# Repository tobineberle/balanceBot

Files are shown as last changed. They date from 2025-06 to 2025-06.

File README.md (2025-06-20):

# balanceBot-v0

## **Introduction**
Over the past few years I have found myself growing increasingly nerdy in all matters engineering related (and trains too for that matter), and it so happens that this interest has had a direct correlation with my desire to build a cool engineering project. I have been fascinated by the [inverted pendulumn problem](https://en.wikipedia.org/wiki/Inverted_pendulum) since my University days, and with some free, unemployed time on my hands I decided to build something influenced by it- the self balancing robot.

### **Goals**
The goal for this project was to build a self-balancing robot from the ground up. No kits, no libraries, no pre-made parts (lets talk about breakout boards later). This was a challenge to approach every aspect of the robot from ground zero with my own engineering decisions and mistakes (so, so many mistakes). There will be stretch goals for subsequent versions of this project but these will be discussed further below under their specific design category. 

### **Parts List**

A quick summary of the parts used. Consumables such as wires and screws are not listed.

| Part Name | Quantity|
|-|-|
|STM32F401RE Nucleo Board | 1 |
|A4988 Stepper Driver | 2|
|SEN0142 MPU6050 Board | 1 |
|SM-42HB34F08AB 12V/1.33A Stepper Motor| 2|
|1998 5MM SHAFT M3 MNTG Hub| 2|

### **Results**
You don't need to scroll all the way down, here is a gif of the robot doing a happy little balancing dance:

Robot

From stress testing it can balance for over five minutes. This is the cutoff where the motors are too hot and the frame begins to melt. It has good setpoint tracking with only minor oscillation and good disturbance rejection (not demonstrated in gif).

### **Next Steps**

Some big future goals I have for the project:
- Integrate all components onto a PCB
- Add bluetooth steering
- Refine the system control (cascade or LRQ)

Stay tuned!

## **Design**

## Mechanical

My approach to the frame design was straightforward: I wanted the robot to be around 20-30cm tall and it needed to be wide enough to accomodate my protoboards. As I have been getting into 3D printing, I chose to design it all in Fusion360. All the following parts were designed in CAD and the stl's are in on github. I won't include the 3D files because I'm pretty sure my file structure/ogranization in them is atrocious.

### **Frame**

I wanted the frame to be modular so that I could print and test the fit of pieces without wasting time or PLA. To accomodate this I added slots on the frame sides so that the middle brackets could slide in. The middle brakets are further secured by pressing a square nut into the holes in each corner before seating them, then screwing them into place. All hardware used to secure the brackets is m3 as its what I had easiest access to.

The middle brackets have slots down the middle for modular mounting of PCBs later. The side brackets have flames down the middle for speed.

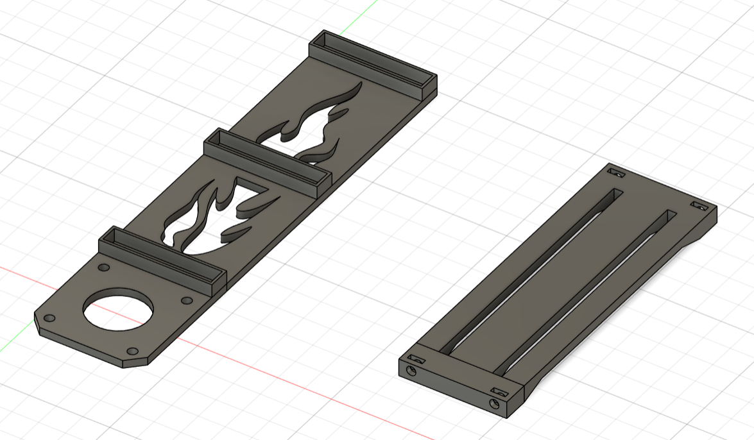
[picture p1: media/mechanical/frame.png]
frame


*Frame Design*

### **Wheels**

Not too much design aspect for the wheels, just had to make sure they fit the aluminium mounting hubs I ordered. 

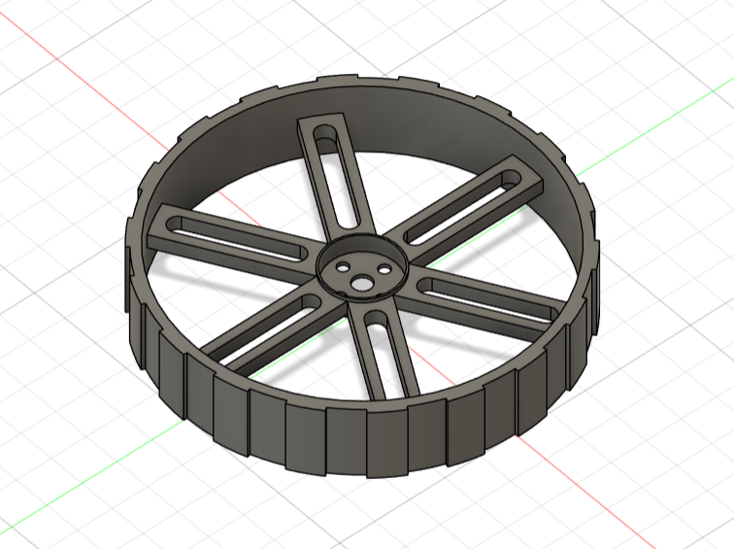
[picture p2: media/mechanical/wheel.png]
wheel


*Wheel Design*

As I was making custom wheels, I needed custom tires to fit them. After researching many methods, the best and most cost effective I found was to make them using hardware store silicone (mono silicone sealant) mixed with cornstarch. Through some messy experimentation, I found a good ratio of silicone to cornstartch was 10:1 and that about 100g silicone + 10g cornstarch was enough to fill my tire molds and had about a 24 hour curing time. The tire mold went through two iterations of design in order to make it easier to remove the tires wihout ripping them. Not many photos here as it was messy.

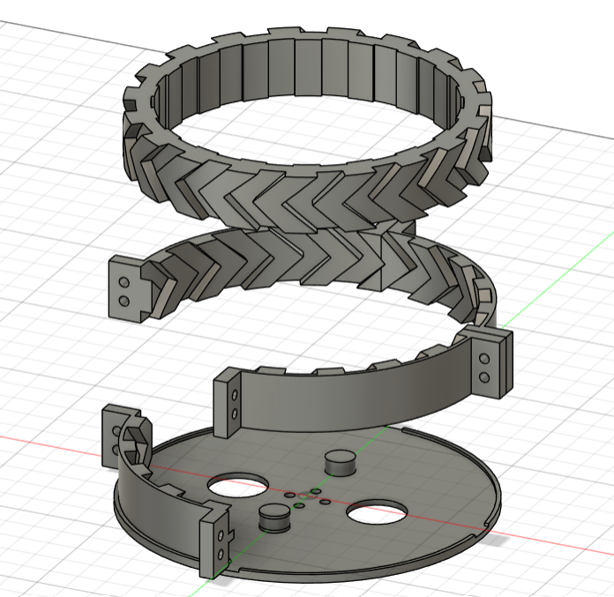
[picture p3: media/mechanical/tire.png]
tire


*Tire/Mold Design*

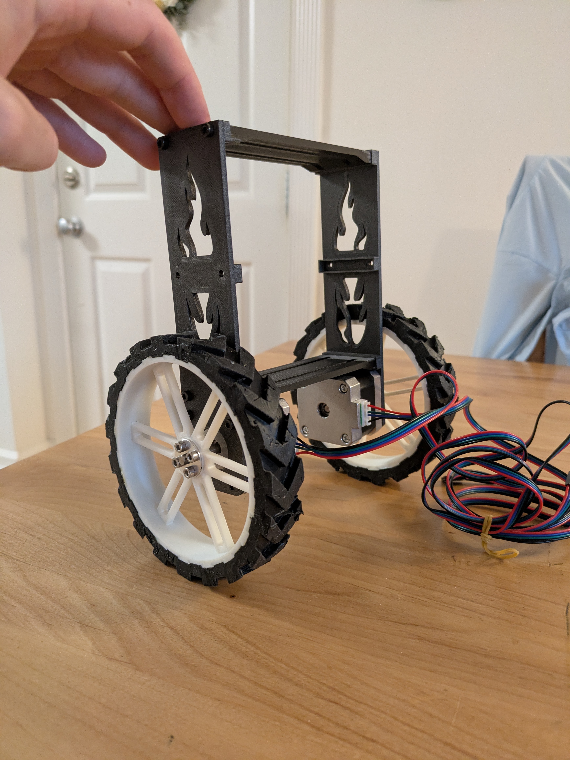
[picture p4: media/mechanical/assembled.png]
assembled


*Assembled Frame*

### **Improvements**

- Frame needs to be printed in a stronger material. The PLA begins to melt after running the motors for more than 5 minutes continuously
- Tires could be redesigned to have less aggresive tread as it would make them easier to remove from the mold. Holy hell taking them out was stressful 
- If I had access to a different material to print the tires with I would 3D print them directly to save hassle
- The mounting bracket system will likely be redesigned for V1 as I get custom PCBs, but it is modular and works well in the meantime

## Electrical

Here is where we talk about using eval boards for components like the A4988 drivers or MPU6050 inertia measurement unit. For V0 of this project, I thought it was more important to get an inital prototype actually working rather then spending months in the weeds doing design work that has already been completed. I have plans to make a microcontroller integrated PCB for the robot, so integrating these other chips would fall within this stretch goal. Good is better than perfect if it means you get stuff done.

### **Part Selection**
#### MicroController

I chose to use STM32 as I wanted to work within an industry accepted environment (sorry arduino). This also meant I got to practice and improve my bare metal programming skills and dry out my eyes reading datasheets. It was also a goal of mine to write libraries for all my components from scratch (except for HAL drivers as I've done this before) and this platform supported this goal by having nothing pre-existing readily available.

#### Motors

NEMA17 stepper motors were chosen due to the ability to directly control their position by commanding steps. To size them properly, I looked for a set that had sufficient torque rating that was over double what I calculated for my robot. I also looked for a higher voltage motor so I could power both the motor and the electronics from one power source.

#### Driver

From research the A4988 is a common motor driver that can support up to ~1.2A of current which is very close to the max rated current of ~1.33A of my motors. 

#### Inertia Measurement Unit

Again, from research the MPU6050 is a common IMU to use. 6DOF was plenty for only neededing to detect pitch and y angle.

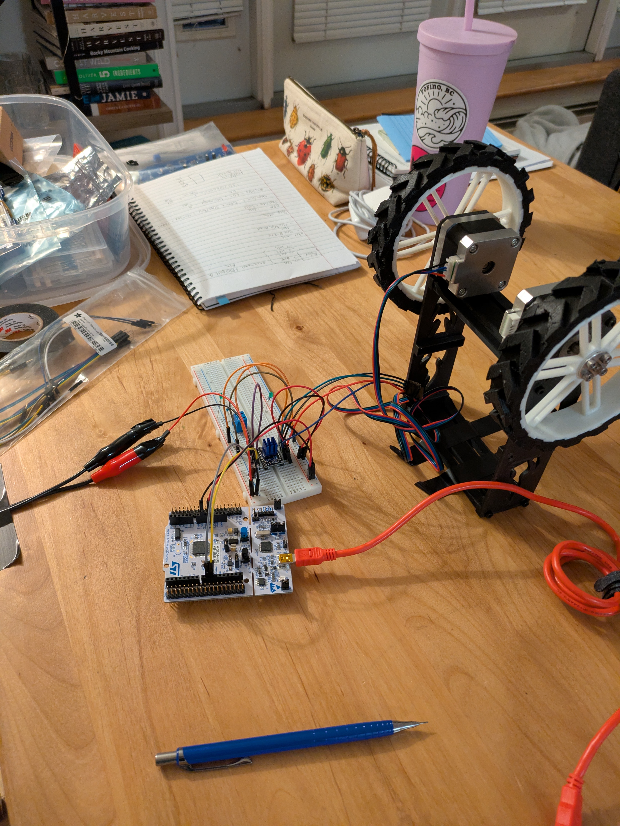
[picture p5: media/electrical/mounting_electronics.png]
elec


*Electronics Breadboarding*

### **Power Distribution**

A little power distribution circuit designed around the LM7805. The LM7805 can regulate up to 30V into 5V which can power the STM32 and peripherals. This lets me run everything from my 12V wall source or a single 4S Lipo battery. LED's are hugely useful for visual feedback that your system is working as intended. This ciruict was soldered onto protoboard along with breakout pins for the A4988 and MPU6050 boards. As mentioned in this sections header, V1 will hopefully incorporate all the components onto a dedicated PCB along with multiple power input methods. Note I only used resistors close to the values shown, just not remembering true values at time of writing this.

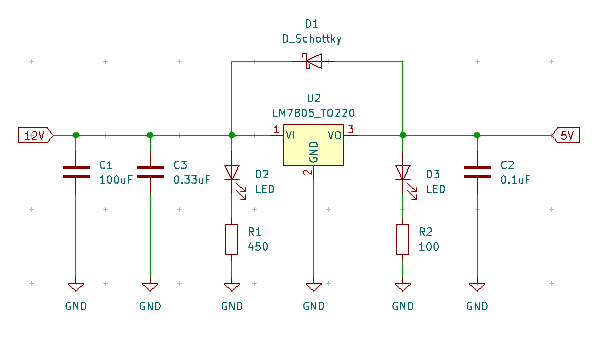
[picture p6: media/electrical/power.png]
power


*Power Distribution using LM7805*

### **Improvements**
- Integrate all components into a single PCB (V1)
- Add multiple methods for power connection and reverse voltage protection
- I haven't actually caluclated a power draw for this sytem yet, so am guessing at the mAh of the batteries I need to order

## Software

Prepare for a long section with diagrams. Writing these libraries and troubleshooting code took propably twice to three times as long as the rest of the project put together. This was probably the most valuable section of the project (so far) for me as it really helped improve my bare metal knowledge. For running a real time control system you need to have around 100-200 Hz loop frequency (5-10 ms loop times).

### **MPU6050 Library**

The MPU6050 communicates with the STM32 over I2C. Sending/reading data from the device is generally easy, using HAL_Read you can read directly from the MPU6050 registers. 

#### Accelerometer and Gryo Data

Straight forward section, just read from registers specified on the MPU6050 datasheet. Simple as.

#### Accelerometer and Gryo Angles

X/Y/Z or Pitch/Yaw/Roll angles can be calculated from your accelerometer and gyro readings. Accelerometer angle is based on trigonometry between the acceleration axises and the gyro angle is based on time elapsed between measurements. Implementations can be found in source code. Rule of thumb for these readings is that angles from your accelerometer will be noisy and angle from you gyro will drift over time. 

#### Kalman Filter Angle

To overcome the noise and drift issues in direct angle calculation, we use the kalman filter. This filter lets us predict the state of a system based on known readings and our estimation of error from both our calculation of the system state and our measurement of the system state. Using a kalman filter is preferable here as values can converge more quickly than averaging over time allowing us to use the filtered angle immediately. As shown below, it is quite amazing how well this works- notice how we have a noisy accelerometer signal and gyro drift and how these are filtered into a smooth signal.

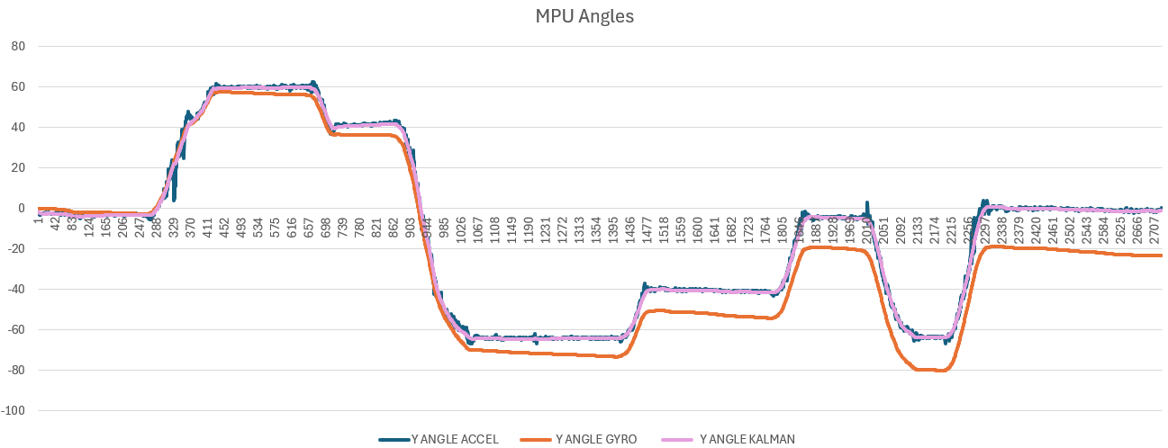
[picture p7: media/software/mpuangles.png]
mpu


*MPU angle comparison*

### **PID Library**

Controls is awesome and if you don't love controls you should because it's awesome. The self balancing robot is technically a non-linear system and thus is a good candidate for a linear quadratic regulator (LQR) which I might implement in a later version. However, PID is also a very reliable method of control and with proper tuning can give excellent results even for non-linear systems. PID is also much simpler to implement in code and I had prior expereince doing it. 

#### PID Updating

This method just updates a PID loop based off its initialzed set point, current value, loop time, and whether we are including derivative filtering. As the block diagram below shows, the code functions as a regular PID loop. Something that is not always common in these systems is the low-pass derivative filtering to smooth noise. From testing, the derivative noise was badly amplified that the robot would shake uncontrollably without any sort of filter on this error. 

Some notes for tuning these gains:

- P: Tune until the robot can catch itself but begins to oscillate back and forth
- D: After P, tune until oscillations are removed and minimized
- I: After D, tune if the robot is drifting in a particular direction. Only tune slightly and if needed.

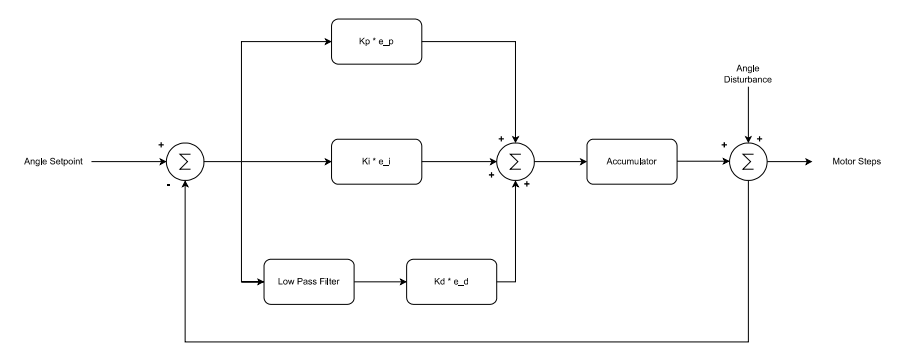
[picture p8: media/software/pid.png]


*PID Control with Low Pass Filtering*

#### Low Pass Filtering

The low pass filter is used to smooth an output based on previous input data. It has an alpha scaling factor from 0.1 (very smooth) to 1 (no smoothing). Some examples of PID logs with and without smoothing are shown below for dramatic impact.

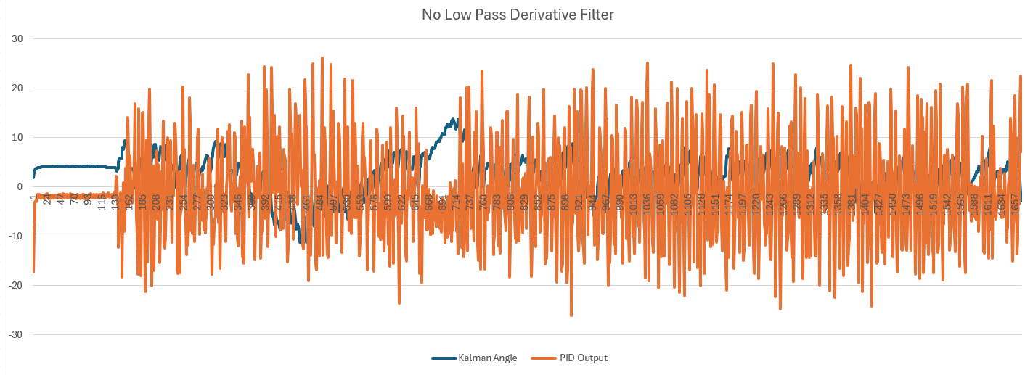
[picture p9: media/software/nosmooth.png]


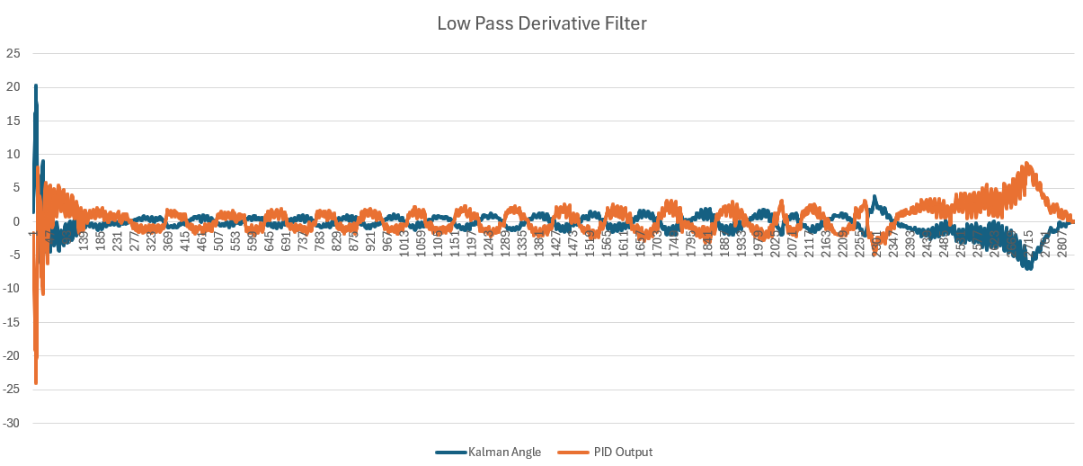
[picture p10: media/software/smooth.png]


*Difference between without and with low pass derivative filtering*

### **A4988 Library**

I wrote an A4988 C library for the STM32F401RE and this helped me get a really good basis of state-based programming, timer setup, and interrupt handling. This was the final piece after implementing the previous two libraries and I thought it would keep going quickly! I was devistatingly wrong. Writing non-blocking motor control code was incredibly tedious, and I spent a lot of time troubleshooting and reading through some other peoples work online. Specifically the following mentions:

[Laurb9's Arduino Cpp Code](https://github.com/laurb9/StepperDriver)

[ErniW's Cpp Code](https://github.com/ErniW/Stepper-motor-bare-metal-STM32)

[Patrick's C Code](https://gitlab.com/rickpat/stm32_a4988)

Now for A4988 operating theory. The A4988 sends motor step when it sees a rising edge on its STEP pin and then needs a 1us settling time before the next pulse. This means the driver can be driven by PWM from the STM32 timer channels or through timer based GPIO triggers. Each of the following different states "modes" controls the PWM frequency in a slightly different way.

For state-based design, I may have gone overboard. Without a pre-planned state diagram, I found myself getting more and more convoluted as my work progressed. The resulting states and their related substates are in the diagram below and I will talk breifly about them in the following sections.

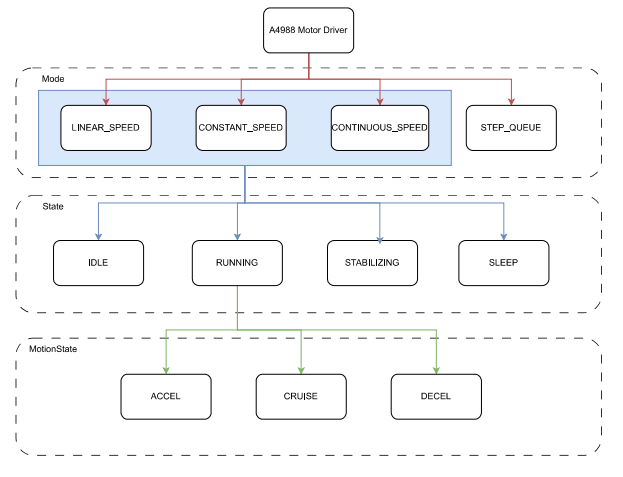
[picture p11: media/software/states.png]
states


*Breakdown of A4988 states and substates*

#### Constant/Linear Speed Modes

This was my first attempt at motor control and was based on what I learned from other motor source code. We set the timer to PWM and then vary the timer length (ARR) to change the motor speed. Every time the motor meets the control capture value it creates an interrupt in which we update parameters such as: position, next cycle speed, steps remaining. While this works really well for time invariant pre-planned moves, it lags in real time systems and was not even remotely close to balancing the bot.

Constant Mode: Send a set number of steps to move and the motor will run at the preset RPM for all steps

Linear Mode: This gives the motor a trapezoidal or triangular speed profile so that it accelerates, cruises, then decelerates over the number of steps you provide it. 

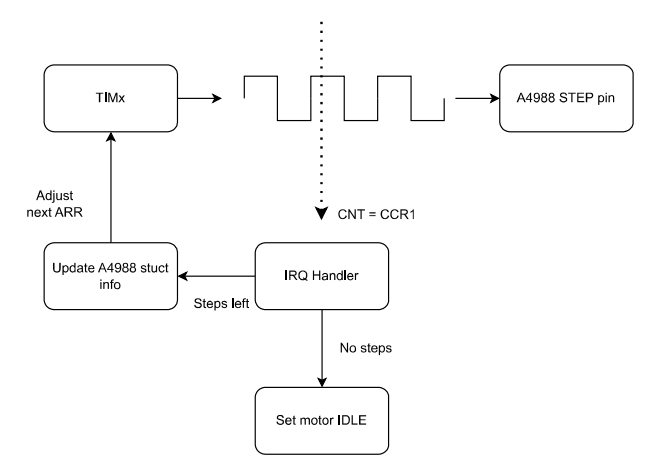
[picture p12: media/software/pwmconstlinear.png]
pwmconstlinear


*Constant/Linear speed diagram*

#### Continuous Speed Mode

The second attempt at motor control was a continuous speed mode, where the motors are constantly running and you just update the RPM. In theory this should work and I probably could've gotten there with it but I ran into MAJOR timer issues. Firstly, I had a timer issue where going from a high -> low rpm would cause the motor to freeze due to the timer ARR not updating and then another CCR event not triggering. I solved this by forcing an auto reload and CNT to 0 so that the timers would function properly for PWM.

This fix caused my second issue in which by forcing a reload and the CNT to 0 I would cut off the PWM cycle of some PWM pulses if my main loop was executing too fast. This was an issue as the main loop needed to run at speeds that prohibited this style of motor control from working at RPM's less than around 30 (depending on microstepping levels). The structure for this looks similar to the diagram in constant/linear. All in all, I probably worked on this mode for 30-40 hours before abandoning it. It still works for continous speed, just not for high update rate applications.

Here are the timing tables I made to diagnose the second issue. These are also useful for if you want to use this mode for some reason and need to know its limits.

*TIMING VALUES FOR REALISTIC RPMS FOR MICROSTEP LEVELS TABLE*
|MS SCALE| MIN ARR 16 Bit [us]| MAX ARR 16 Bit [us]| MIN ARR 32 Bit [us] | MAX ARR 32 Bit [us]
|- |- | -| -| -|
| 1 | 1500 | 60000 | 1500 | 300000 |
| 1/2 | 750 | 50000 | 750 | 150000 |
| 1/4 | 375 | 37500 | 375 | 75000 |
| 1/8 | 187 | 37500 | 187 | 37500 |
| 1/16 | 93 | 18750|  93 | 18750 |

#### Step Queue Mode

The holy grail of motor control. After a lot more research and pondering I started step queue method. By running a timer at a constant frequency (10KHz) and using the IRQ handler to choose when to toggle the output pin (i.e. use GPIO instead of TIMx Channels) we can control the amount of steps we are taking almost in real time. The kicker here is that the IRQ handler needs to be fast:

 ```"Interrupts shall be quick and simple"```

 When we mean fast, we mean on the order of a few us, as there is only 100us inbetween interrupt calls. For this, I stripped down my IRQ handler to the essentials and used some atomic functions and direct register writes to make the process faster.

 <img src="./media/software/stepq.png" alt="stepq" width="600"/>

*Step Queue diagram*

FINALLY success! As a final safety precaution, I created another table to limit the number of steps fed into the step queue for each iteration of the main loop, effectively capping the maximum RPM. The below table shows the max steps allowed to queue for different max RPMs at different main loop speeds [Hz]. This is showed for sixteenth microstepping and the values vary for different resolutions of full steps.

 <img src="./media/software/maxrpm.png" alt="maxrpm" width="600"/>

*Step Queue Max RPM for 1/16 Microstepping*

### **Improvements**
- I'm just going to spend a month in a hole refactoring my code and bug testing

 <img src="./media/workstation.png" alt="workstation" width="600"/>

*Cozy workstation shot if you made it this far*

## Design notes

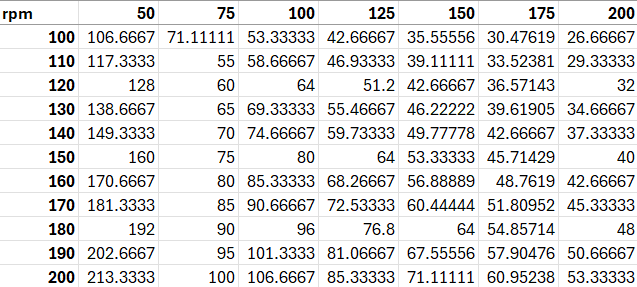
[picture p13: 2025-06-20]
media/software/maxrpm.png

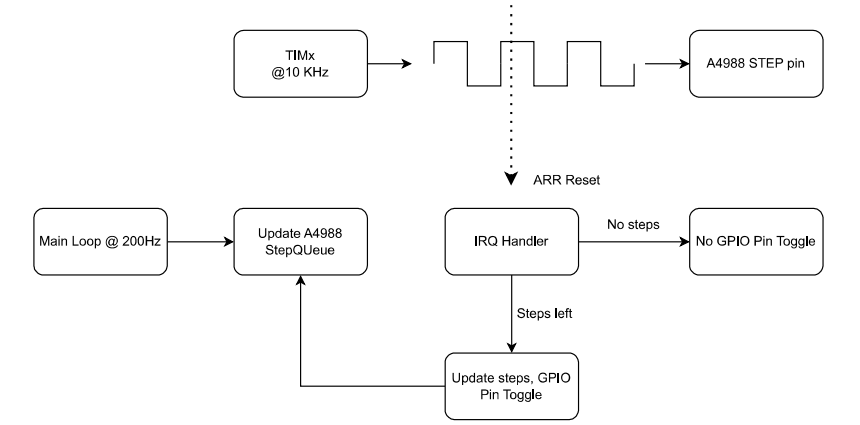
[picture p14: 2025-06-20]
media/software/stepq.png

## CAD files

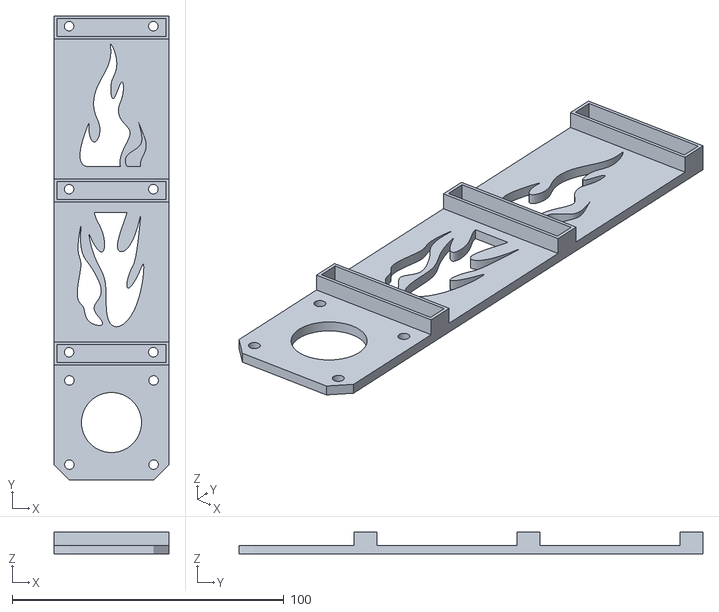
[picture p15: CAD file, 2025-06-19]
Models/Frame/frame-v1.stl
42.3 x 170.8 x 8.00

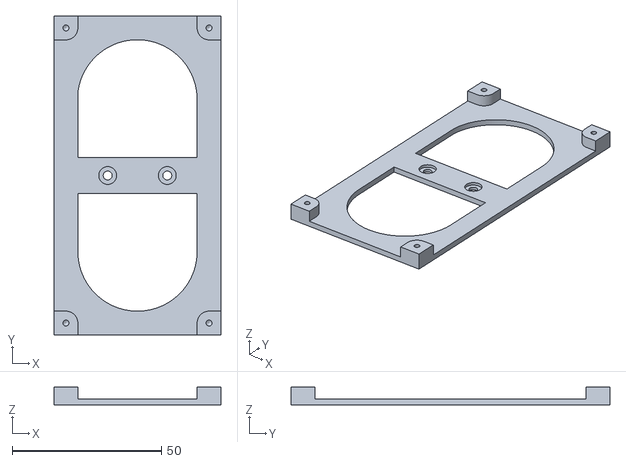
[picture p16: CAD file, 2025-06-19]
Models/PCB Mounts/pcb_mount_v0.stl
56.0 x 107.0 x 6.00

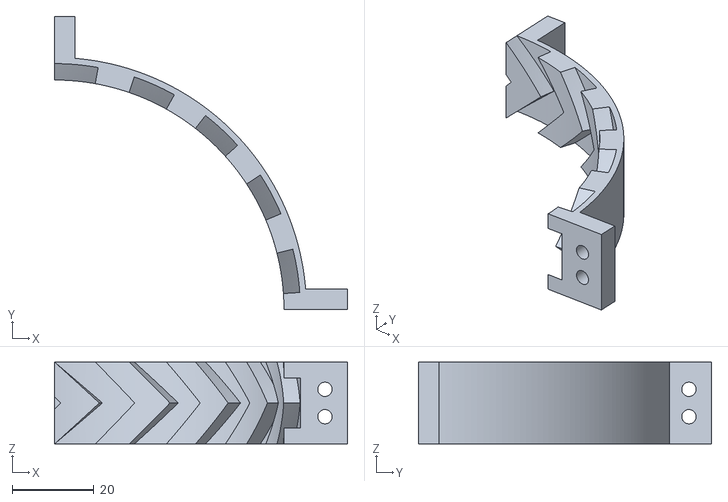
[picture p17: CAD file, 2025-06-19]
Models/Wheels/side-mold-I-v0.stl
71.5 x 71.5 x 20.0

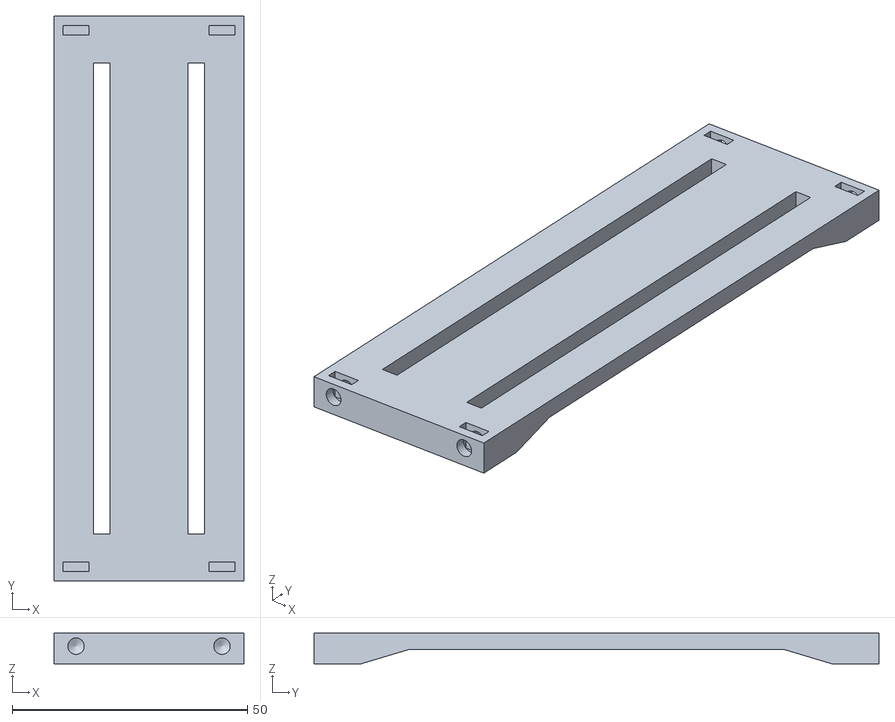
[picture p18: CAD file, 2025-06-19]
Models/Frame/mount-bracket-v1.stl
40.3 x 120.0 x 6.50

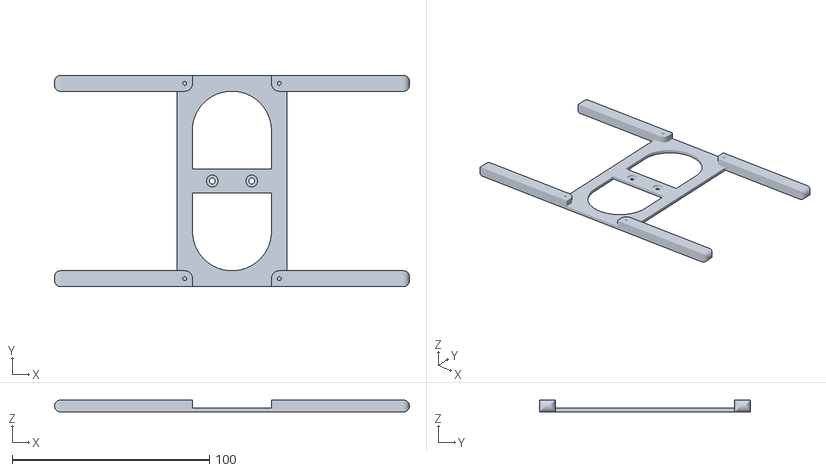
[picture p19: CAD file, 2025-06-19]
Models/PCB Mounts/pcb_mount_arms.stl
180.0 x 107.0 x 6.00

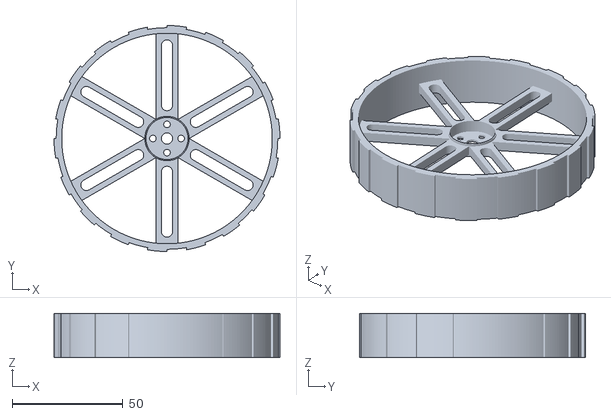
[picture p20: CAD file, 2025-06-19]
Models/Wheels/wheel_v1.stl
102.0 x 102.0 x 20.0

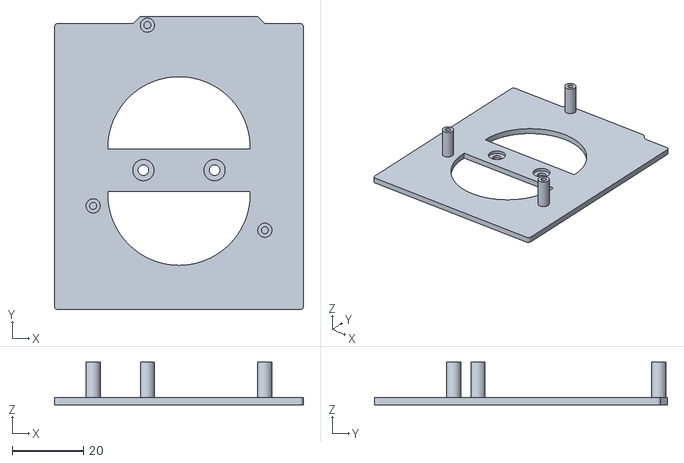
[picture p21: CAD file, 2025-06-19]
Models/PCB Mounts/stm_mount_v0.stl
70.0 x 82.5 x 12.0

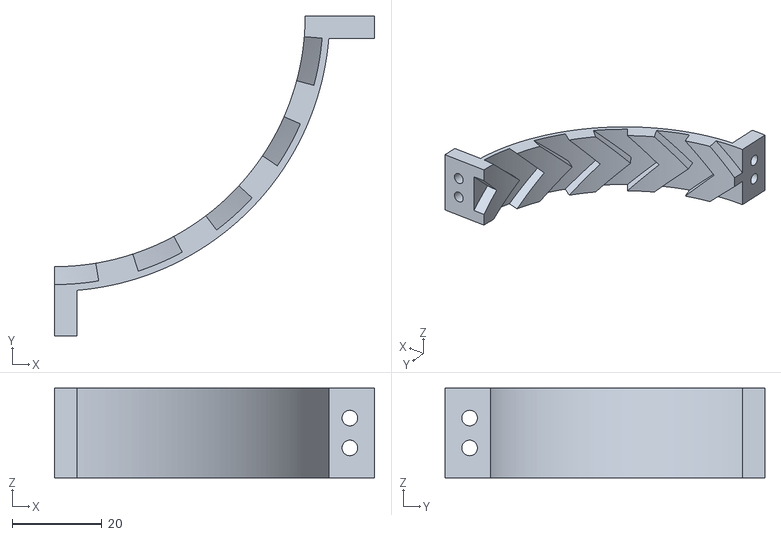
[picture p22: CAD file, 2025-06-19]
Models/Wheels/side-mold-IV-v0.stl
71.5 x 71.5 x 20.0

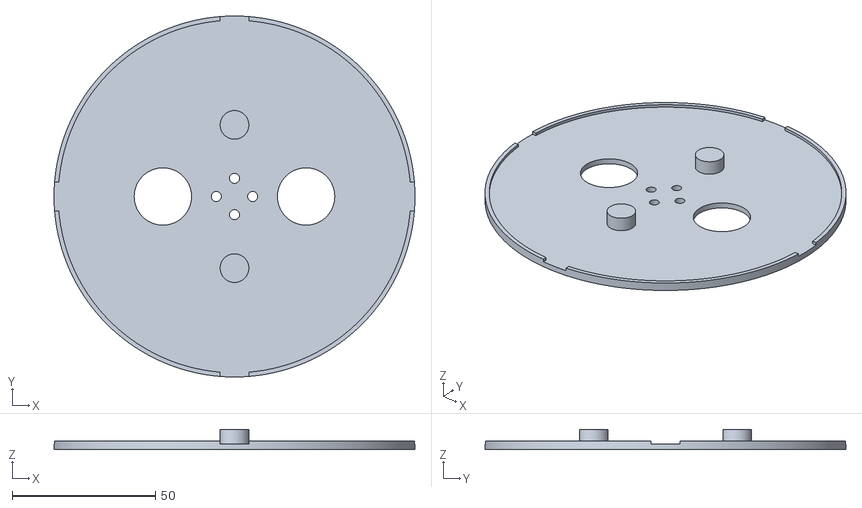
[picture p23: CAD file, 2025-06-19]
Models/Wheels/top-bottom-mold-v1.stl
126.0 x 126.0 x 7.00

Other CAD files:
Models/Wheels/side-mold-III-v0.stl
Models/Wheels/side-mold-II-v0.stl

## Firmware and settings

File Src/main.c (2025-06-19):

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
/* Includes ------------------------------------------------------------------*/
#include "main.h"

/* USER CODE BEGIN Includes */
//#include <a4988.h>
#include <mpu6050.h>
#include <stdio.h>
#include <stdlib.h>
#include <A4988.h>
#include <pid.h>

/* USER CODE END Includes */

I2C_HandleTypeDef hi2c1;

TIM_HandleTypeDef htim1;
TIM_HandleTypeDef htim2;
TIM_HandleTypeDef htim3;

/* USER CODE BEGIN PV */
A4988_t motA;
A4988_t motB;
MPU6050_t mpu;
PID_t pid;
volatile uint32_t irq_counter = 0;


/* USER CODE END PV */

void SystemClock_Config(void);
static void MX_GPIO_Init(void);
static void MX_I2C1_Init(void);
static void MX_TIM2_Init(void);
static void MX_TIM3_Init(void);
static void MX_TIM1_Init(void);
/* USER CODE BEGIN PFP */
void I2C1_RESET(I2C_HandleTypeDef* hi2cx);

/* USER CODE END PFP */

/**
  * @brief  The application entry point.
  * @retval int
  */
int main(void)
{

  /* MCU Configuration--------------------------------------------------------*/

  /* Reset of all peripherals, Initializes the Flash interface and the Systick. */
  HAL_Init();

  /* Configure the system clock */
  SystemClock_Config();

  /* Initialize all configured peripherals */
  MX_GPIO_Init();
  MX_I2C1_Init();
  MX_TIM2_Init();
  MX_TIM3_Init();
  MX_TIM1_Init();
  /* USER CODE BEGIN 2 */

  //Motor Init
  A4988_init(&motA, GPIOA, GPIO_PIN_4, STEP_QUEUE);
  A4988_StepQ_timer_init(&motA, TIM2, TIM2_IRQn, HAL_RCC_GetPCLK1Freq(), 100, GPIOA, GPIO_PIN_0);
  A4988_microstepping_init(&motA, GPIOC, GPIO_PIN_10, GPIOC, GPIO_PIN_11, GPIOC, GPIO_PIN_12);
  A4988_setMicrostepResolution(&motA, SIXTEENTH);

  A4988_init(&motB, GPIOC, GPIO_PIN_1, STEP_QUEUE);
  A4988_StepQ_timer_init(&motB, TIM3, TIM3_IRQn, HAL_RCC_GetPCLK1Freq(), 100, GPIOA, GPIO_PIN_6);
  A4988_microstepping_init(&motB, GPIOB, GPIO_PIN_4, GPIOB, GPIO_PIN_5, GPIOB, GPIO_PIN_6);
  A4988_setMicrostepResolution(&motB, SIXTEENTH);

  //MPU Init
  I2C1_RESET(&hi2c1);
  MPU6050_init(&mpu, &hi2c1, A2G, G250DPS);

  //PID Init
  //target, kp, ki, kd, -lim, + lim
  PID_init(&pid, 0, 0.24, 0, 0.048, -40, 40);
  /* USER CODE END 2 */

  /* Infinite loop */
  /* USER CODE BEGIN WHILE */
  uint32_t tick = HAL_GetTick();
  float accumulator = 0;
  float prev_output = 0;
  float output = 0;

  printf("Kalman Angle, PID Output, Accumulator\n");
	  while (1)
	  {
		  //1Hz => 10000 IRQ calls
		  //Need at least 100Hz for good response time
		  float now_tick = HAL_GetTick();
		  uint32_t loop_time =  now_tick - tick;
		  if(loop_time >= 5){
			  //Time updates
			  tick = now_tick;

			  //MPU updates
			  float y_angle = MPU6050_getAccAngleDegY(&mpu);
			  float pitch = MPU6050_getGyroX(&mpu);
			  float kalman_angle = MPU6050_getKalmanAngleDeg(&mpu, loop_time, y_angle, pitch);

			#if 1
			  /**
			   * Added d error filter to PID
			   */
			  //PID updates, scale using PID in init
			  output += PID_update(&pid, kalman_angle, loop_time, 0.1);
			  int32_t steps = (int32_t)output;
			  output -= steps;
			  printf("%.4f, %.4f\n", kalman_angle, output);
			  A4988_queueSteps(&motA, steps);
			  A4988_queueSteps(&motB, steps);
			#endif

			#if 0
			  /**
			   * Low pass filter testing
			   */
			  //Removed Low pass filter for now
			  output = PID_update(&pid, kalman_angle, loop_time);
			  accumulator += PID_lowPassFilter(output, prev_output, 0.3);
			  prev_output = output;
			  //Ensure motor steps are full int
			  int32_t steps = (int32_t)accumulator;
			  //Logging
			  printf("%.4f, %.4f, %.4f\n", kalman_angle, output, accumulator);
			  accumulator -= steps;
			  A4988_queueSteps(&motA, steps);
			  A4988_queueSteps(&motB, steps);
			#endif
		  }

    /* USER CODE END WHILE */
    /* USER CODE BEGIN 3 */
  }
  /* USER CODE END 3 */
}

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
/* USER CODE BEGIN 4 */
void I2C1_RESET(I2C_HandleTypeDef* hi2cx){
	HAL_StatusTypeDef conn = HAL_I2C_IsDeviceReady(hi2cx, (MPU6050_ADDRESS <<1) + 0, 1, 100);
	if (conn != HAL_OK){
		HAL_I2C_DeInit(hi2cx);
		GPIO_InitTypeDef GPIO_InitStruct = {0};
		GPIO_InitStruct.Pin = GPIO_PIN_8;
		GPIO_InitStruct.Mode = GPIO_MODE_OUTPUT_PP;
		GPIO_InitStruct.Pull = GPIO_NOPULL;
		GPIO_InitStruct.Speed = GPIO_SPEED_FREQ_LOW;
		HAL_GPIO_Init(GPIOB, &GPIO_InitStruct);
		HAL_GPIO_WritePin(GPIOB, GPIO_PIN_8, GPIO_PIN_RESET);
		for(int i = 0; i < 10; i ++){
			HAL_GPIO_WritePin(GPIOB, GPIO_PIN_8, GPIO_PIN_SET);
			HAL_Delay(20);
			HAL_GPIO_WritePin(GPIOB, GPIO_PIN_8, GPIO_PIN_RESET);
			HAL_Delay(20);
		}
		MX_I2C1_Init();
	}
}


/* USER CODE END 4 */
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


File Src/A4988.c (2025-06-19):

/*
 * A4988.c
 *
 *  Created on: Jun 2, 2025
 *      Author: tobin
 */

#include "A4988.h"

/**
 * @brief 	Initialize the minimum requirements to use the motor. Defaults to no microstepping
 * @note	MUST call A4988_timer_init to finish motor setup, and must call init_microstepping to enable microstepping
 *
 * @param	dirPort is the port for direction
 * @param	dirPin is the pin for the dirPort
 * @param	mode can be either CONSTANT_SPEED or LINEAR_SPEED
 * @retval	An initialized motor object
 */
void A4988_init(A4988_t* motor, GPIO_TypeDef* dirPort, uint16_t dirPin, uint8_t mode)
{
	//Pins
	motor->_dirPort = dirPort;
	motor->_dirPin = dirPin;
	//Default no microstepping
	motor->_microStepsPerRev = 200;
	motor->_rpm = 0;
	motor->_sps = 0;
	motor->_resolution = FULL;
	motor->_state = IDLE;
	motor->_stabilizeCounter = 0;
	motor->_position = 0;
	motor->_totalSteps = 0;
	motor->_stepsRemaining = 0;
	motor->_accelSteps = 0;
	motor->_decelSteps = 0;
	motor->_cruiseSteps = 0;
	motor->_speedProfile._mode = mode;
	motor->_speedProfile._accelRate = 500;
	motor->_speedProfile._decelRate = 500;

	switch(mode){
	case CONSTANT_SPEED:
		motor->_irqHandler = _A4988_IRQ_constantSpeed;
		break;
	case LINEAR_SPEED:
		motor->_irqHandler = _A4988_IRQ_linearSpeed;
		break;
	case CONTINUOUS_SPEED:
		motor->_irqHandler = _A4988_IRQ_continuousSpeed;
		break;
	case STEP_QUEUE:
		motor->_irqHandler = _A4988_IRQ_stepQ;
		break;
	}
	_A4988_enableTIM_IRQ(motor);
}

/**
 * @brief	Initializes the timer to drive the step pin
 *
 * @param	motor object initialized
 * @param 	timer chosen for running the motor (eg TIM2)
 * @param	timerChannel for the timer (1)
 * @param 	timerInt is for interrupt, needs the IRQn (eg TIM2_IRQn)
 * @param	APBClockFreq is clock frequency of your APB bus
 */
void A4988_timer_init(A4988_t* motor, TIM_TypeDef* timer, uint8_t timerChannel, IRQn_Type timerInt, uint32_t APBClockFreq)
{
	//Init timer
	motor->_timer = timer;
	motor->_timerChannel = timerChannel;
	motor->_timerInt = timerInt;

	//Configuring timer
	//Disable counter
	motor->_timer->CR1 &=~ TIM_CR1_CEN;
	//Set pre-scaler for 1us tick
	motor->_timer->PSC = (APBClockFreq / 1000000) - 1;
	//Initialize ARR, this value doesn't matter and will change
	motor->_timer->ARR = 5000;
	//The value to be compared to TIMx counter and signaled on OC1 output
	//This is active duty cycle and needs to be longer than our A4988 settling time of 1us
	motor->_timer->CCR1 = MIN_PULSE_LENGTH;

	//Sets 0x6, enabling PWM mode 1
	//Channel x is active as long as TIMx->CNT < CCR1
	if(motor->_timerChannel == 1)      motor->_timer->CCMR1 |= TIM_CCMR1_OC1M_1 | TIM_CCMR1_OC1M_2;
	else if(motor->_timerChannel == 2) motor->_timer->CCMR1 |= TIM_CCMR1_OC2M_1 | TIM_CCMR1_OC2M_2;
	else if(motor->_timerChannel == 3) motor->_timer->CCMR2 |= TIM_CCMR2_OC3M_1 | TIM_CCMR2_OC3M_2;
	else if(motor->_timerChannel == 4) motor->_timer->CCMR2 |= TIM_CCMR2_OC4M_1 | TIM_CCMR2_OC4M_2;

	//Clear interrupt flags
	motor->_timer->SR = 0;
	//Capture compare interrupt enable
	motor->_timer->DIER |= 1 << motor->_timerChannel;
	//Enable timer
	motor->_timer->CR1 |= TIM_CR1_CEN;
	}

/**
 * @brief	Initializes the timer to drive the step pin for step queue mode
 * @note	DO NOT CALL RPM SETTING OR MOVE FUNCTIONS AFTER INITIALZING THIS WAY AS YOU WILL RESET ARR AND THROW OFF TIMER IRQ CALLS
 * @note	DONT ASK HOW LONG IT TOOK TO FIGURE THAT ONE OUT
 *
 * @param	motor object initialized
 * @param 	timer chosen for running the motor (eg TIM2)
 * @param 	timerInt is for interrupt, needs the IRQn (eg TIM2_IRQn)
 * @param	APBClockFreq is clock frequency of your APB bus
 * @param	motorClockPeriod in us
 * @param	port for stepping
 * @param	pin for stepping
 */
void A4988_StepQ_timer_init(A4988_t* motor, TIM_TypeDef* timer, IRQn_Type timerInt, uint32_t APBClockFreq, uint32_t motorClockPeriod, GPIO_TypeDef* stepPort, uint16_t stepPin){
	//Init timer
	motor->_timer = timer;
	motor->_timerChannel = 0;
	motor->_timerInt = timerInt;
	motor->_timer->CR1 &=~ TIM_CR1_CEN;
	motor->_timer->PSC = (APBClockFreq / 1000000) - 1;
	motor->_timer->ARR = motorClockPeriod - 1;
//	motor->_timer->PSC = 0;
//	motor->_timer->ARR = 1599;
	motor->_timer->EGR = TIM_EGR_UG;
	//IRQ on ARR value
	motor->_timer->DIER |= TIM_DIER_UIE;
	motor->_timer->CR1 |= TIM_CR1_CEN;
	_A4988_enableTIM_IRQ(motor);

	//Init Step pin
	//Medium speed for faster response, the switching speed should be 25MHz
	GPIO_InitTypeDef GPIO_InitStruct = {0};
	motor->_stepPort = stepPort;
	motor->_stepPin = stepPin;
	HAL_GPIO_WritePin(stepPort, stepPin, GPIO_PIN_RESET);
	GPIO_InitStruct.Pin = stepPin;
	GPIO_InitStruct.Mode = GPIO_MODE_OUTPUT_PP;
	GPIO_InitStruct.Pull = GPIO_NOPULL;
	GPIO_InitStruct.Speed = GPIO_SPEED_FREQ_MEDIUM;
	HAL_GPIO_Init(stepPort, &GPIO_InitStruct);
}

/**
 * @brief	Initializes microstepping, to use microstepping call set_microsteps
 *
 * @param	motor object initialized
 * @param	MSxPort port for x microstepping pin
 * @param	MSxPin	pin corresponding to the MSxPort
 */
void A4988_microstepping_init(A4988_t* motor, GPIO_TypeDef* MS1Port, uint16_t MS1Pin, GPIO_TypeDef* MS2Port, uint16_t MS2Pin, GPIO_TypeDef* MS3Port, uint16_t MS3Pin)
{
	motor->_MS1Port = MS1Port;
	motor->_MS1Pin = MS1Pin;
	motor->_MS2Port = MS2Port;
	motor->_MS2Pin = MS2Pin;
	motor->_MS3Port = MS3Port;
	motor->_MS3Pin = MS3Pin;
}

/**
 * @brief 	Sets up the reset, sleep, and enable pins
 * @note	This could probably be broken up into individual inits
 *
 * @param	motor object initialized
 * @param	xxxPort port for the corresponding function
 * @param 	xxxPin pin for the corresponding port
 */
void A4988_alt_states_init(A4988_t* motor, GPIO_TypeDef* RSTPort, uint16_t RSTPin, GPIO_TypeDef* SLPPort, uint16_t SLPPin, GPIO_TypeDef* ENPort, uint16_t ENPin)
{
	motor->_RSTPort = RSTPort;
	motor->_RSTPin = RSTPin;
	motor->_SLPPort = SLPPort;
	motor->_SLPPin = SLPPin;
	motor->_ENPort = ENPort;
	motor->_ENPin = ENPin;
}

/**
 * @brief 	Enables the interrupt for the timer
 *
 * @param	motor object initialized
 */
void _A4988_enableTIM_IRQ(A4988_t* motor)
{
	NVIC_EnableIRQ(motor->_timerInt);
}

/**
 * @brief	Starts the motor after calling a move.
 * 			Will only start when motor is IDLE and after STABILIZING is completed
 * @note	This sets the CCxE bit of TIMx which toggles whether the signal is output on the corresponding output pin
 *
 * @param	motor pointer
 */
void _A4988_start(A4988_t* motor)
{
	motor->_state = RUNNING;
	//Reset timer and force ARR to update
	//Question: will this allow moves to overwrite?
	//CNT/EGR might need to be moved back to the run method
	motor->_timer->CNT = 0;
	motor->_timer->EGR |= TIM_EGR_CC1G;
	//Connect timer to output pin (ARMED)
	motor->_timer->CCER |= 1 << (motor->_timerChannel - 1) * 4;
}
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

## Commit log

2025-06-12 errors with continuous speed mode
    [A4988.c, main.c]
2025-06-13 fixed TIM2 motor bug, refactor IRQ handler
    [A4988.c, main.c, mpu6050.c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]
2025-06-19 version-1 complete
    [frame-v1.stl, mount-bracket-v1.stl, pcb_mount_arms.stl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]
2025-06-19 version-0 complete
    [frame-v1.stl, mount-bracket-v1.stl, pcb_mount_arms.stl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]

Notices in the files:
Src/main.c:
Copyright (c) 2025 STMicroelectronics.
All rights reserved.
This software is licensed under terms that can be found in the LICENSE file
